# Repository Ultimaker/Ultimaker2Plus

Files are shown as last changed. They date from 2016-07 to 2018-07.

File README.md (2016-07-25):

# Ultimaker 2+
Bill of Materials and parts for Ultimaker 2+

In this repository you will find the documentation and source files for all parts in the Ultimaker 2+ 3D printer. In the Bill Of Materials (BOM) directory all the parts are numbered and named with the correct amounts and raw materials. 9407 is a subsystem, which has a separate BOM. 

The electronic files can be found in the following directories: 1155-F Print Table Heated Bed; 1249-B Ulticontroller board and 1546-A Ultimainboard V2.1.4.

If you are missing a part or information feel free to file an issue on github.

Harma Woldhuis <br>
Ultimaker Productmanager Hardware

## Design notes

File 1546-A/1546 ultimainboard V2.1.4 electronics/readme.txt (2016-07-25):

The UltiMainboard 2.x.x electronics are released under GPLv2 license.
And are based on the origonal Ultimaker electronics design by Jan-Jaap Schuurman, Siert Wijnia and ErikDeBruijn at http://reprap.org/wiki/Ultimaker's_v1.5.7_PCB
As well as the ArduinoMega2560 by Arduino: http://arduino.cc/en/Main/arduinoBoardMega2560

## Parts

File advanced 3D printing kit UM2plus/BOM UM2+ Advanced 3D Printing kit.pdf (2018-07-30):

## 9521 UM2+ Advanced 3D Printing kit

Total quantity parts | 14
Partnummer | | Name | Quantity
1462 | A | door clip top | 2
1463 | A | door clip bottom | 2
1464 | A | door plate UM2+ | 1
1470 | A | build plate adhesion surface | 1
2152 | A | hex socket head remform screw 2.5 x 6 | 4
2278 | A | TFM Isolator Coupler | 2
2313 | C | olsson nozzle 0.40 | 2

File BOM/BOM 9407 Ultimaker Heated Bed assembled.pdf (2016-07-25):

## SubBOM

Total quantity parts | 39
Partnummer | Naam | Quantity | Material
1125 | A | Table Spring DR2150 | 3 | RVS 302
1153 | B | Print Table Base Plate | 1 | EN AW-6082
1155 | F | Print Table Heated Bed | 1 | several
1170 | B | Square Flanged Linear Bearing LMK12LUU | 2 | several
1183 | F | Heated Bed Cable | 1 | several
1187 | A | Trapezoidal Lead Nut | 1 | RG 7
1202 | B | ISO 7380 M3x10 | 6 | AISI 304
1206 | B | ISO 7380 M3x20 | 1 | AISI 304
1214 | A | ISO 7040 Nut M3 Prev. torque A2 | 4 | AISI 304
1217 | A | ISO 7380 M4x10 A2 | 8 | AISI 304
1243 | B | Heated Bed Cable Clip | 1 | ABS
1256 | A | Build Platform Glass Retainer Back | 2 | stainless steel
1257 | B | Knurled Nut Platform | 3 | RVS 304
1288 | A | Washer M6 | 3 | stainless steel
1987 | C | Table Clip Front-Left | 1 | RVS verenbandstaal AISI 301
1988 | C | Table Clip Front-Right | 1 | RVS verenbandstaal AISI 301

## 9407 Ultimaker Heated Build Platform Assembled

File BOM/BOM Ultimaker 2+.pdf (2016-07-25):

9501

Total quantity
parts | 325
Partnummer | Rev | Name | Quantity | Material
1011 | D | Y-linear shaft | 2 | 1.4034 (X46Cr13)
1012 | D | X-linear shaft | 2 | 1.4034 (X46Cr13)
1024 | E | Limit Switch, Black Short Wire | 1 | several
1056 | A | Sintered Bushing | 4 | Sintered Bronze
1065 | B | Linear Bearing LM6LUU | 2 | several
1069 | A | Tube Coupling Collet | 2 | Nylon
1071 | A | Clamp Clip | 2 | Nylon
1156 | A | Z-shaft Cap Bottom | 2 | PC ABS
1159 | D | Z-Motor with Trapezoidal Lead Srew | 1 | several
1161 | G | LED Strip Cold white | 1 | several
1162 | C | Limit Switch, Blue Wire | 1 | several
1163 | C | Limit Switch, Red Wire | 1 | several
1165 | B | Timing Pulley 5mm Shaft GT2 | 2 | Aluminum
1166 | C | Timing Pulley 8mm Shaft GT2 | 8 | Aluminum
1167 | E | Timing Pulley Double 8mm Shaft GT2 | 1 | Aluminum
1168 | B | Sliding Block Spring | 4 | DIN 17.223 material nr. 1.1200
1169 | E | Z-linear Shaft | 2 | 1.4034 (X46Cr13)
1171 | B | Double flat Cable 10 Wire | 1 | several
1172 | A | Print Head Shaft X | 1 | 1.4034 (X46Cr13)
1173 | A | Print Head Shaft Y | 1 | 1.4034 (X46Cr13)
1176 | A | Spacer 8.2x10x5 | 2 | Nylon
1177 | A | Spacer 8.2x10x10 | 4 | Nylon
1178 | A | Spacer 8.2x10x25 | 1 | Nylon
1182 | B | X,Y Motor | 2 | several
1186 | E | Print Head Cable | 1 | several
1188 | A | Timing Belt GT2 200 | 2 | several
1189 | A | Timing Belt GT2 610 | 4 | several
1200 | A | ISO 7380 M3x8 | 4 | AISI 304
1201 | C | Washer Large M3 | 8 | AISI 304
1202 | B | ISO 7380 M3x10 | 16 | AISI 304
1203 | B | ISO 7380 M3x12 | 14 | AISI 304
1204 | B | ISO 7380 M3x16 | 40 | AISI 304
1205 | B | ISO 7380 M3x14 | 2 | AISI 304
1206 | B | ISO 7380 M3x20 | 1 | AISI 304
1207 | B | ISO 7380 M3x25 | 12 | AISI 304
1209 | C | Nut M3 | 5 | AISI 304
1213 | B | DIN 562 Square Nut M3 A2 | 36 | AISI 304
1214 | A | ISO 7040 Nut M3 Prev. torque A2 | 8 | AISI 304
1220 | A | Ball Bearing F688-2RS | 8 | stainless steel
1230 | E | Front Panel UM2 | 1 | dibond
1231 | J | Back Panel UM2 | 1 | dibond
1232 | D | Left Panel UM2 | 1 | perspex
1233 | C | Right Panel UM2 | 1 | perspex
1234 | F | Bottom Panel UM2 | 1 | dibond (Alu/PP/Alu)
1235 | E | Top Panel UM2 | 1 | dibond (Alu/PP/Alu)
1240 | C | Main Board Electronics Cover | 1 | Steel El.Galvanized

## Ultimaker2+ voor assemblage

1241 | B | Motor Spacer UM2 | 2 | PC ABS
1242 | A | Spacer 3.2 x 6x 10 | 4 | Nylon
1244 | A | Knob Front UM2 | 1 | ABS 757
1245 | A | Knob Housing UM2 | 1 | PC 2807 Makrolon
1247 | A | Display Oled Blue | 1 | several
1249 | B | Ulticontroller Board | 1 | several
1250 | B | SD card 4G | 1 | several
1251 | B | Ulticontroller Electronics Cover | 1 | sheet metal DC01-A-m acc. EN10130
1255 | A | Sliding Block Half UM2 | 8 | PC ABS
1266 | C | Bowden tube | 1 | PFA
1273 | C | Cable Cover | 2 | sheet metal DC01-A-m acc. EN10130
1279 | C | Feeder Ring | 1 | AISI 304
1281 | C | Braided Sleeve Clip | 5 | ABS
1287 | A | Washer M7 | 1 | AISI 304
1294 | A | Keep Hands Clear Sticker | 1 | plastic
1306 | C | Hot end holder bottom | 1 | ALU 3.2315
1307 | C | Hot end holder top | 1 | ALU 3.2315
1308 | C | Cooling Rib Hot End | 1 | ALU 3.2315
1310 | B | Hot end Isolator | 1 | AISI 303
1313 | A | Model Cooling Fan 12VDC 0.1 A | 2 | several
1315 | A | Jumper | 2 | several
1321 | C | Print Head Middle | 1 | PA6-GF30
1322 | D | Print Head Bottom | 1 | PA6-GF30
1325 | A | Insert material sticker | 1 | plastic
1326 | A | Warning sticker | 1 | plastic
1330 | C | Hot-end Cooling Fan 5VDC 0.08A | 1 | several
1348 | A | ISO 7380 M3x4 A2 | 4 | AISI 304
1351 | A | ISO 4762 M2,5x10 | 2 | AISI 304
1354 | A | ISO 724 Hex nut M7 | 1 | AISI 304
1362 | A | Tap Fix 2.5x14 mm staal verzinkt bolkop porzidrive | 8 | steel
1363 | A | Ferrite Core | 2 | Ferrite
1521 | A | Short Print Head Thumb Screw | 4 | steel
1546 | A | Ultimainboard V2.1.4 | 1
1748 | D | Print head top single hole | 1 | PA6-GF30
1960 | G | Grip Axis | 1 | AISI 303
1961 | A | Idler Spring | 1 | DIN 17.224 material nr. 1.4310
1962 | E | Tension Indicator | 1 | POM-GF10
1963 | N | Feeder casing Part A-left | 1 | POM-GF10
1965 | N | Feeder casing Part B-left | 1 | POM-GF10
1967 | M | Feeder lever part A | 1 | POM-GF10
1968 | J | Feeder lever part B | 1 | POM-GF10
1969 | F | spur gear 1M 11T | 1 | PA6
1970 | E | spur gear 1M 36T | 1 | PA6
1971 | C | Threaded standoff | 2 | AISI 304
1972 | C | idler wheel | 1 | AISI 303
1973 | A | bearing idler wheel | 1 | stainless steel
1974 | A | bearing feeder axis | 2 | stainless steel
1976 | D | Filament Guide Insert | 1 | POM-GF10
1977 | B | Feeder Motor | 1 | several
2048 | A | Din 914 M4x4 Set screw | 11 | AISI 304
2275 | C | Isolator Spacer 9.4 mm | 1 | Alu type 5000 or 6000
2278 | A | TFM Isolator Coupler | 1 | TFM

2282 | B | Print Table Back Cover | 1 | Dibond
2283 | C | Heater Cartridge 24V 35W | 1 | several
2284 | B | Fan Bracket | 1 | AISI 304
2288 | B | PT 100B sensor glassfiber | 1 | several
2311 | E | olsson heater block | 1 | brass MS58
2313 | C | olsson nozzle 0.40 | 1 | brass MS58
2317 | B | M3x16 countersunk pozidrive | 1 | AISI 304
2322 | A | Nozzle ring DIN 6798V M3 | 1 | AISI 304
9129 | A | SD card sticker | 1 | plastic
9407 | A | Ultimaker Heated Build Platform Assembled | 1 | several

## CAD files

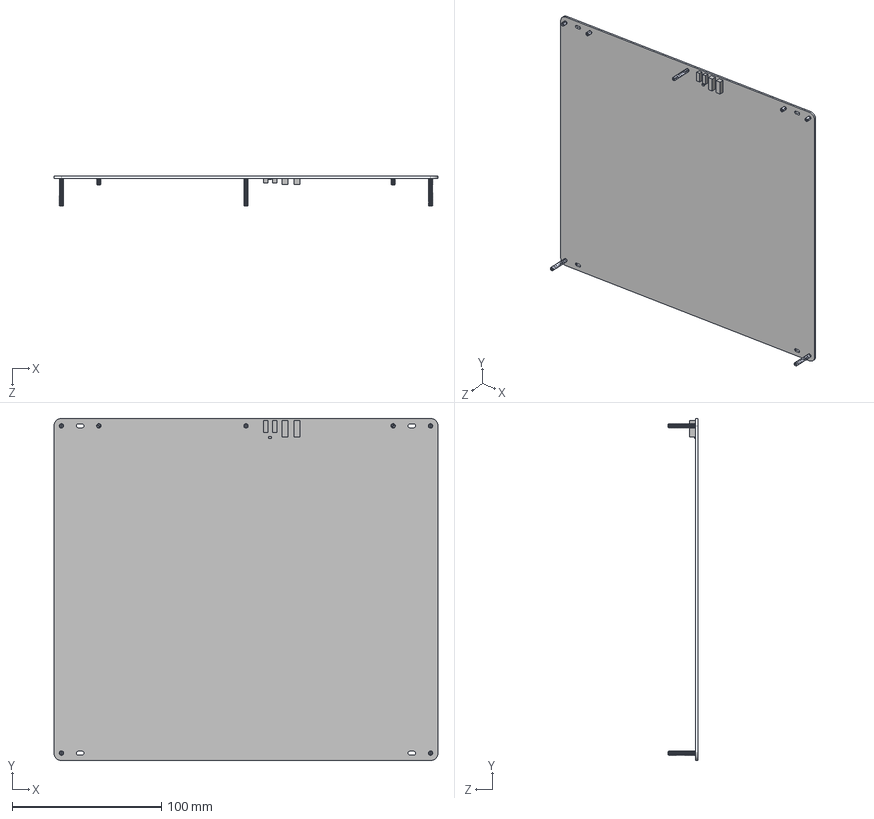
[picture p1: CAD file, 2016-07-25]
1155-F/1155-F.STEP
257.0 x 229.0 x 20.0 mm
1155-D
FH-M3-xZI_FH-M3-6ZI x 4
FH-M3-xZI_FH-M3-20ZI x 3

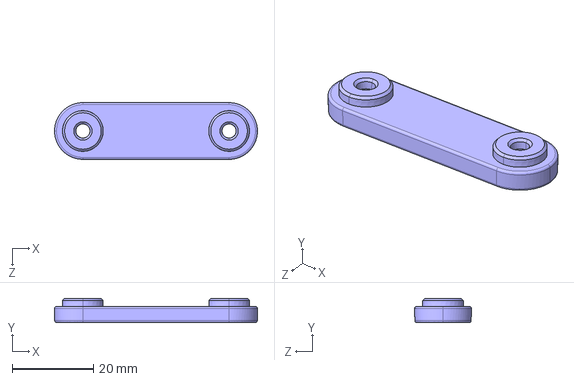
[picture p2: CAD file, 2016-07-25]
1156-A.STEP
50.0 x 6.00 x 14.0 mm

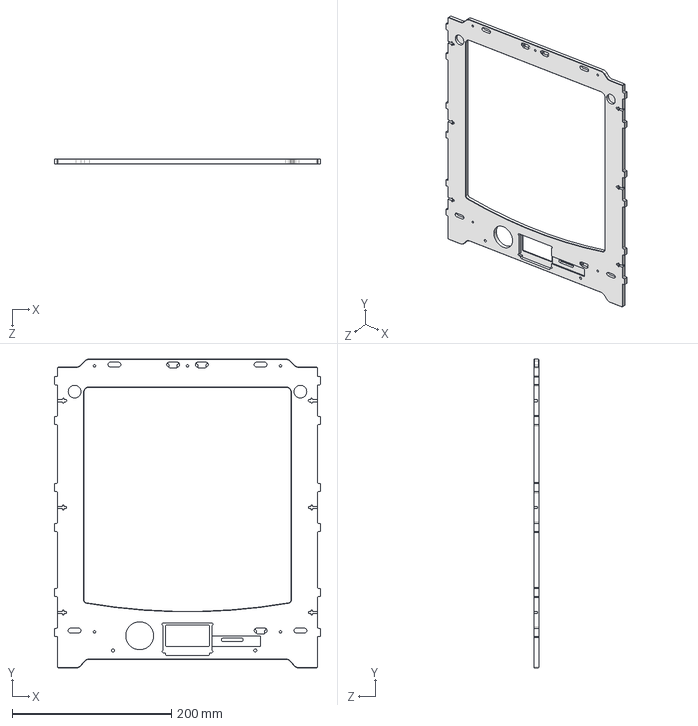
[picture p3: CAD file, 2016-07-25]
1230-E/1230-E.STEP
334.2 x 388.0 x 6.20 mm

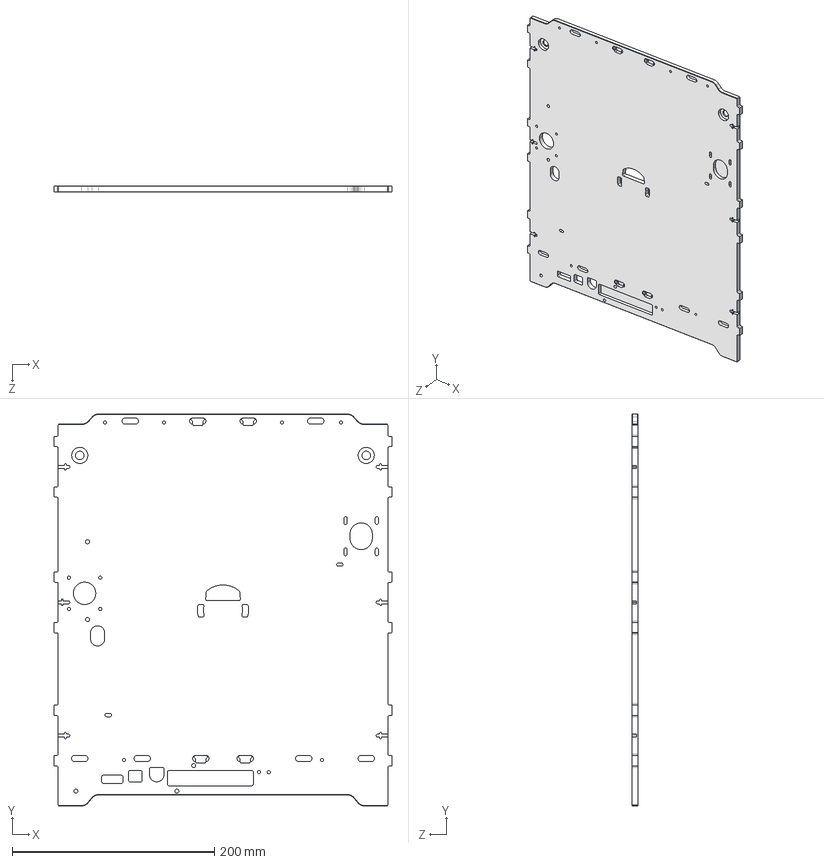
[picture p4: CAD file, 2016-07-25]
1231-J/1231-J.STEP
334.2 x 388.0 x 6.00 mm

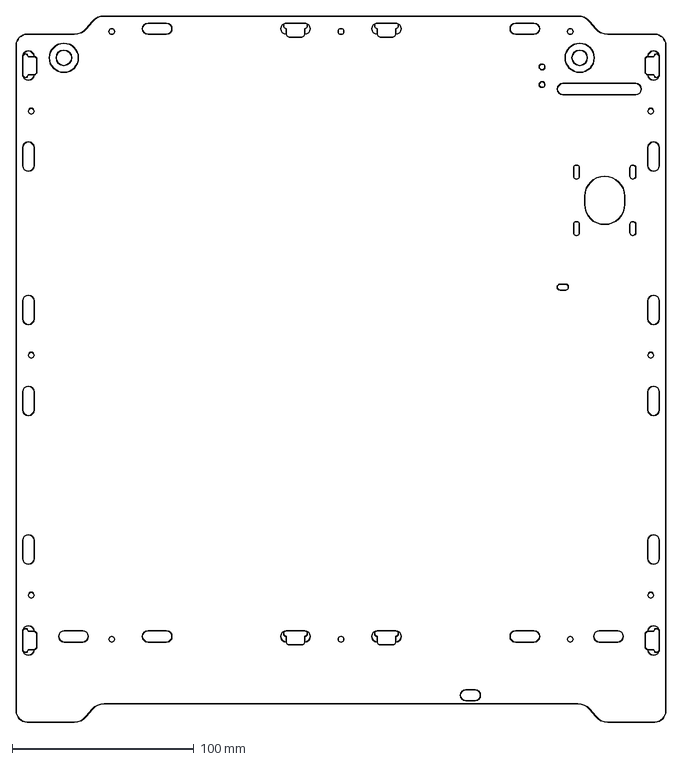
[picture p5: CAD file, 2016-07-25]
1232-D/1232-D Binnenkant.DXF
357.0 x 388.0 mm

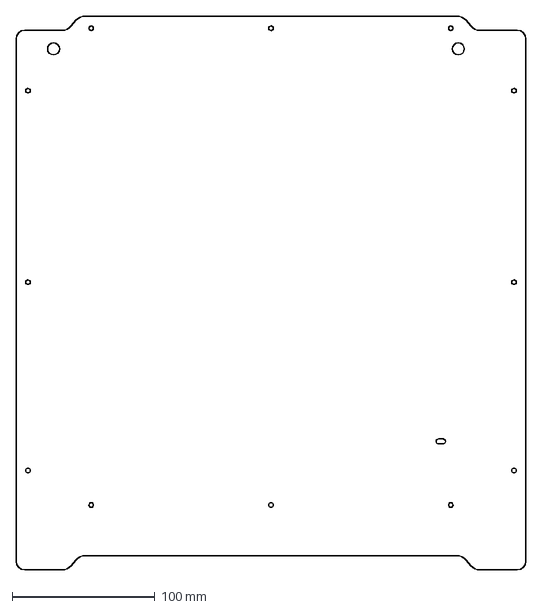
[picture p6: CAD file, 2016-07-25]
1233-C/1233-C Buitenkant.DXF
357.0 x 388.0 mm

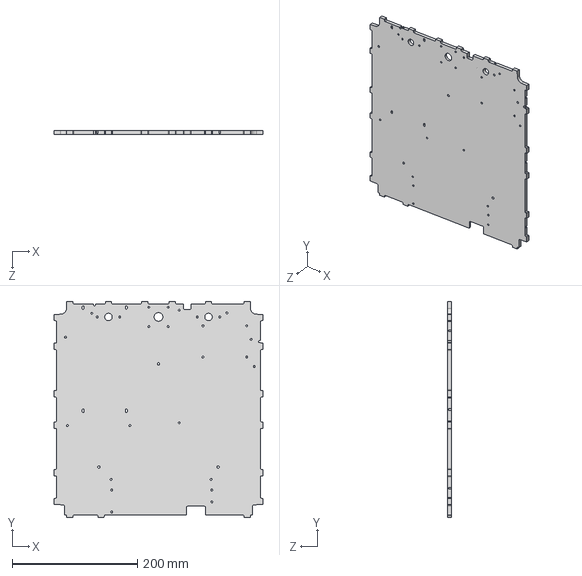
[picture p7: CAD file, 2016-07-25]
1234-F/1234-F.STEP
334.2 x 345.6 x 6.00 mm

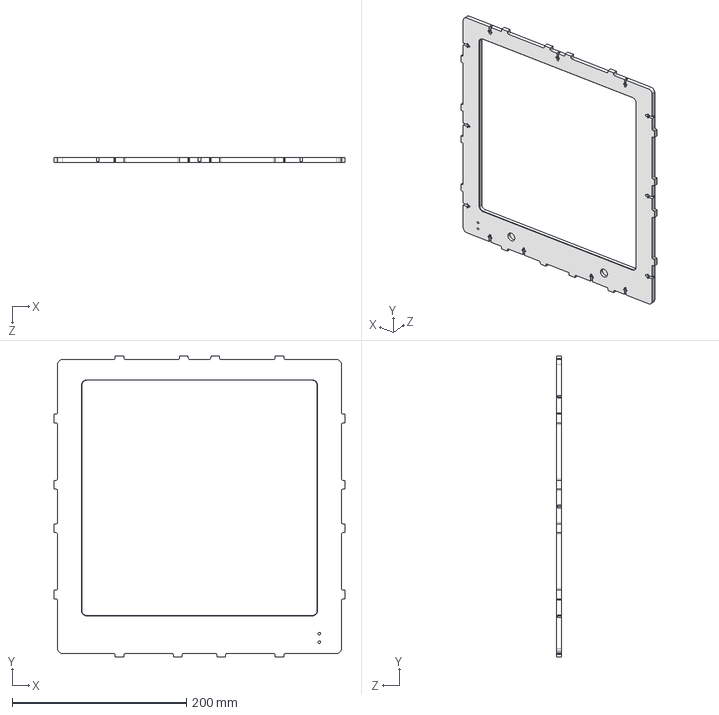
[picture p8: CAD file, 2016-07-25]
1235-E/1235-E.STEP
334.2 x 345.6 x 6.00 mm

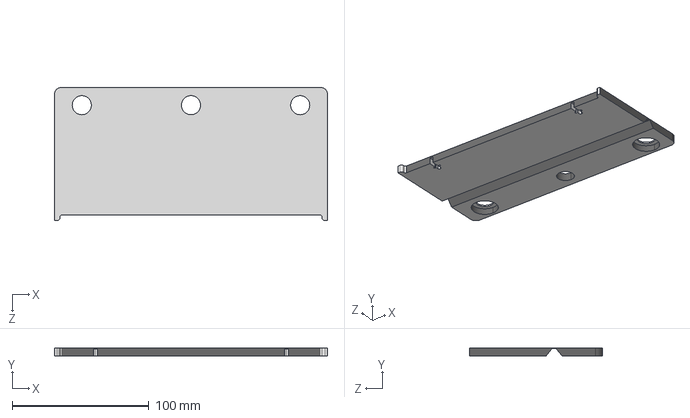
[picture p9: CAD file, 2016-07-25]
2282-B/2282-B.STEP
200.0 x 6.10 x 97.5 mm

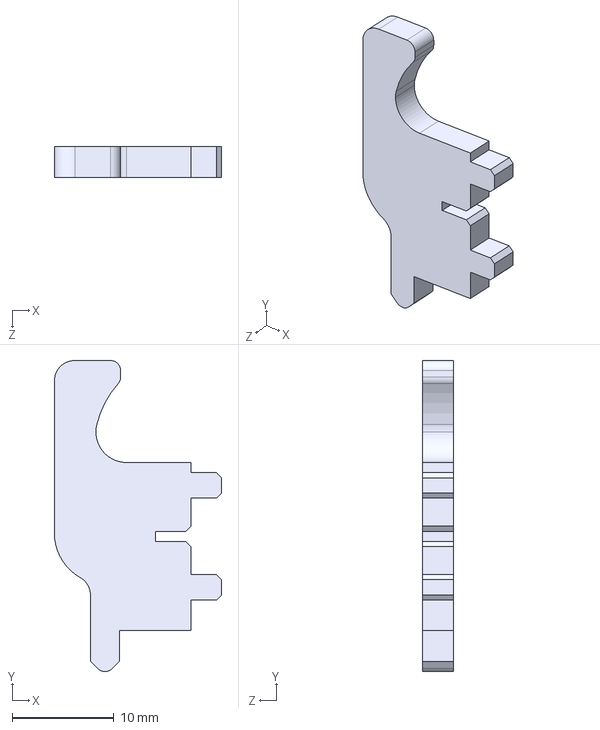
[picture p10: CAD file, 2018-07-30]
advanced 3D printing kit UM2plus/1462/1462-A.STEP
16.4 x 30.5 x 3.00 mm

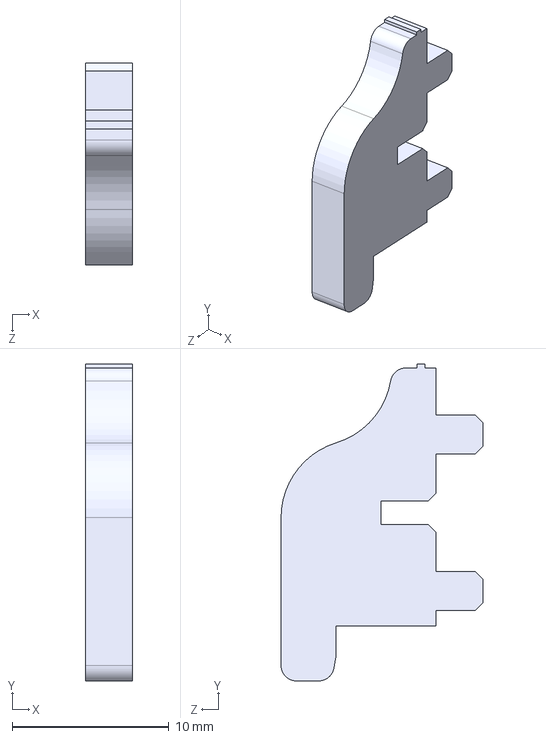
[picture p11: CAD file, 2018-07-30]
advanced 3D printing kit UM2plus/1463/1463-A .STEP
3.00 x 20.3 x 12.9 mm

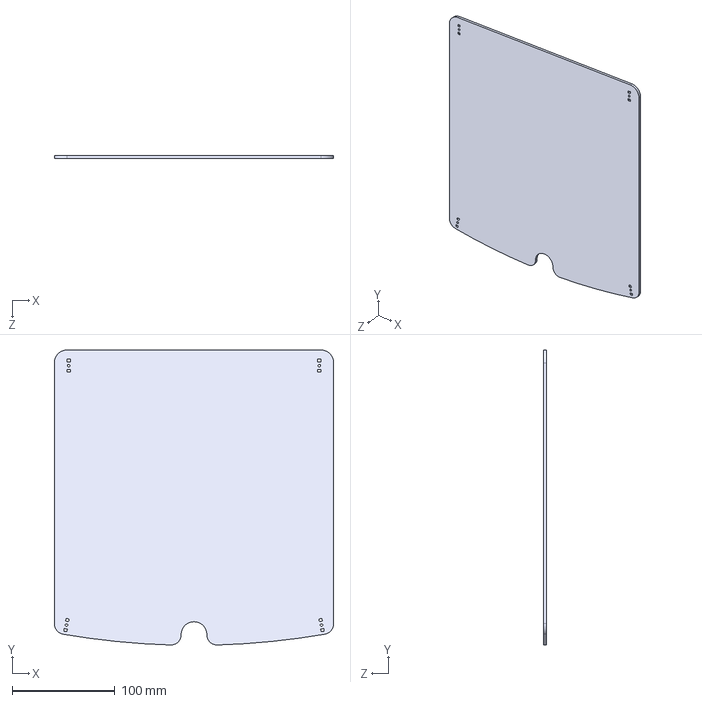
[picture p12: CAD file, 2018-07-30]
advanced 3D printing kit UM2plus/1464/1464-A.STEP
272.0 x 287.2 x 3.00 mm

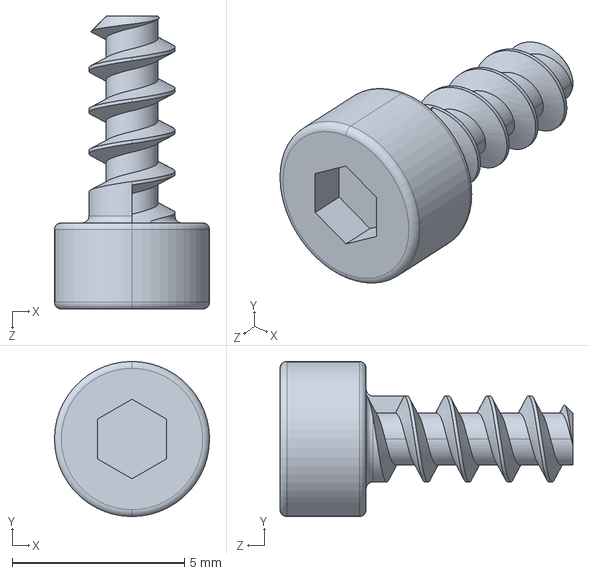
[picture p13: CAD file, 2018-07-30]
advanced 3D printing kit UM2plus/2152/2152-A.STEP
4.50 x 4.50 x 8.50 mm

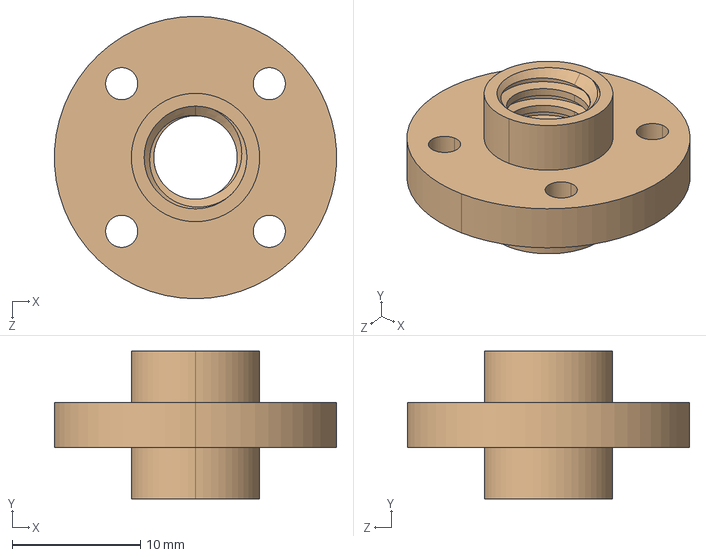
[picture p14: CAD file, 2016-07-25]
1187-A.STEP
22.0 x 11.5 x 22.0 mm

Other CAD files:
1232-D/1232-D.STEP
1233-C/1233-C.STEP
1232-D/1232-D Buitenkant.DXF
1233-C/1233-C Binnenkant.DXF
1011-D.STEP
1012-D.STEP
1024-E.STEP
1056-A.STEP
1065-B.STEP
1069-A.STEP
1071-A.STEP
1125-A.STEP
1153-B.STEP
1161-G.STEP
1162-C.STEP
1163-C.STEP
1165-B.STEP
1166-C.STEP
1167-E.STEP
1168-B.STEP
1169-E.STEP
1170-B.STEP
1172-A.STEP
1173-A.STEP
1176-A.STEP
1177-A.STEP
1178-A.STEP
1182-B.STEP
1183-F.STEP
1188-A.STEP
1189-A.STEP
1200-A.STEP
1201-C.STEP
1202-B.STEP
1203-B.STEP
1204-B.STEP
1205-B.STEP
1206-B.STEP
1207-B.STEP
1209-C.STEP
1213-B.STEP
1214-A.STEP
1217-A.STEP
1220-A.STEP
1230-E/1230-E.DXF
1231-J/1231-J.DXF
1234-F/1234-F.DXF
1235-E/1235-E.DXF
1240-C.STEP
1241-B.STEP
1242-A.STEP
1243-B.STEP
1244-A.STEP
1245-A.STEP
1247-A.STEP
1250-B.STEP
1251-B.STEP
1255-A.STEP
1256-A.STEP
1257-B.STEP
1266-C.STEP
1273-C.STEP
1279-C.STEP
1281-C.STEP
1287-A.STEP
1288-A.STEP
1294-A.STEP
1306-C.STEP
1307-C.STEP
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

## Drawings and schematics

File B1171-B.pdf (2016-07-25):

# Ultimaker Original

## Heat shrink to protect

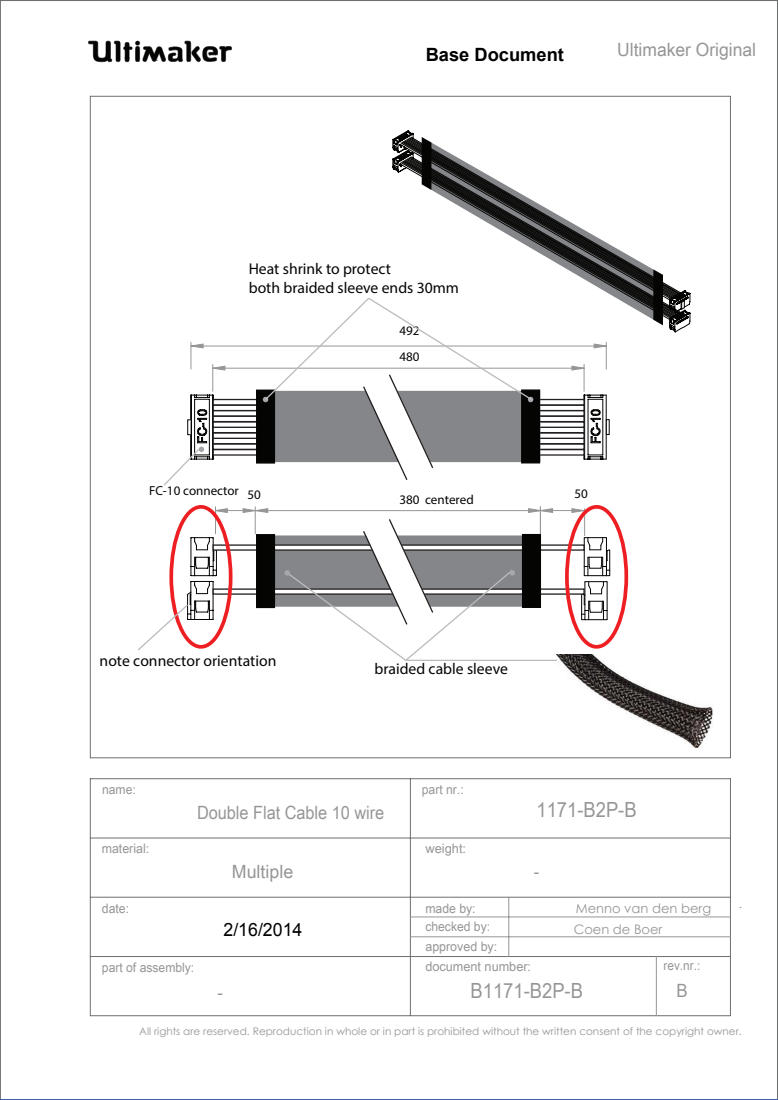
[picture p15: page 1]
Multiple; name:; material:; date:; part of assembly:; rev.nr.:; part nr.:; made by:; weight:; approved by:; checked by:; document number: B1171-B2P-B; 380 centered; FC-10 connector; Base Document

both braided sleeve ends 30mm

note connector orientation

braided cable sleeve

Double Flat Cable 10 wire

Menno van den berg
Coen de Boer

All rights are reserved. Reproduction in whole or in part is prohibited without the written consent of the copyright owner.

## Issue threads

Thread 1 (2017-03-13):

Logos and graphics

dintid, 2017-03-13:
Hello,
I wondered if there are some reasons the logo (robot for the sides) and other graphics like SD and on/off is not included in the repositories as high res png/pdf files?

They might of course be under some different license, but please let us know :)
I found the "Ultimaker" logo using your forums but/and I can't browse the file-structure, so can't look for other usefull graphics files
https://ultimaker.com/download/2381/Ultimaker%20Corporate%20Design%20Manual.pdf

Looking forward to hearing from you (mailed a week ago, but havn't heard back)

Cheers

harmawoldhuis, 2017-03-13:
Hello dintid,

We put the files we use to order the parts in the repositories. It could be that it isn't very high resolution. Please find attached the high res png files of our logo with robot. You can cut the robot from there.
If you need any other high res grafics, please let me know.

Kind regards,
Harma Woldhuis
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

daid, 2017-03-14:
There is also the font which contains these as vectors:
http://software.ultimaker.com/ULTIMAKER-FONT.TTF

Ghostkeeper, 2017-03-14:
I traced the logo once as SVG.
[ultimaker.svg.zip](https://github.com/Ultimaker/Ultimaker2Plus/files/840968/ultimaker.svg.zip)

dintid, 2017-03-15:
Thanks!
Is there any files with the SD-card + the enclosing bracket and on/off?

daid, 2017-03-15:
Just wondering, what are you planning to do with these?

dintid, 2017-03-16:
Just trying to make my machine as close as possible to the real deal :)

Closed 2017-03-13.

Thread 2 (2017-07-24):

Duplicate component in file "Main assembly Ultimaker 2+"

Spirou42, 2017-07-24:
Inside the file: "Main assembly Ultimaker 2+" there is a duplicate component in the sub component: "Feeder left_fil flow sens/fedder handler" there are two components named "1967-M_part B (1968)" and "1968-J_part B (1968)". Those two components are identical and occupy the same space.

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

BagelOrb, 2017-07-25:
Paging @Bas-van-Deursen

harmawoldhuis, 2017-07-26:
updated assembly, removed obsolete part

Closed 2017-07-26.

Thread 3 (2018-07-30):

top and bottom clips Advanced 3D Printing Kit missing

wybren1971, 2018-07-30:
Hello,

I was looking through the repro of de ultimaker 2 and 2+ but could not find the step file for the top and bottom clip of the front enclosure coming with the advanced 3d printing kit..

Is it possible to add these to the repository or in an repository of their own?

thanks in advance
Wybren

harmawoldhuis, 2018-07-30:
Hello Wybren,

I've just added the files to the repository.

Kind regards,
Harma Woldhuis

wybren1971, 2018-07-31:
Super Harma,

Bedankt voor de snelle actie.

Groet Wybren

Closed 2018-07-30.

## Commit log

2016-07-25 initial commit
    initial commit
    [1011-D.STEP, 1012-D.STEP, 1024-E.STEP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]
2017-07-26 updated feeder assembly
2018-07-30 advanced 3D printing kit
    added files
    [1462-A.DXF, 1462-A.STEP, 1463-A .DXF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]
